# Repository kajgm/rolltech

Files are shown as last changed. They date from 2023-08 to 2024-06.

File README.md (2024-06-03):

# Rolltech - Chairable

Roll Technology presents Chairable, a revolutionary product designed to explore the immature field of spherical wheel technology.

- Chairable utilizes a spherical wheel design for tight maneuvering and a space-efficient footprint
- Leverages an adjustable clamping mechanisim to enable modular attachment to a variety of office chairs
- A large 7000mAh lithium polymer battery and a powerful 2200W motor provide the ability to move a 125kg load at a 2.5m/s pace
- Uses a carefully crafted mechanical design implemented with machined steel and custom 3D printed elements
- A safe and robust experience is achieved through a fully enclosed electrical circuit with 14+ motor control, logic, and safety elements
- Operated remotely using a tailored PCB design, a custom controller casing, and a specifically crafted low-power circuit.

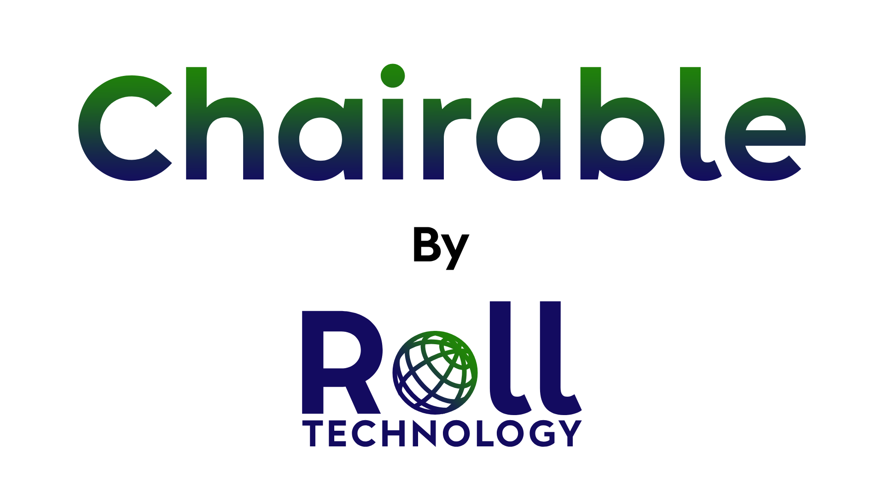
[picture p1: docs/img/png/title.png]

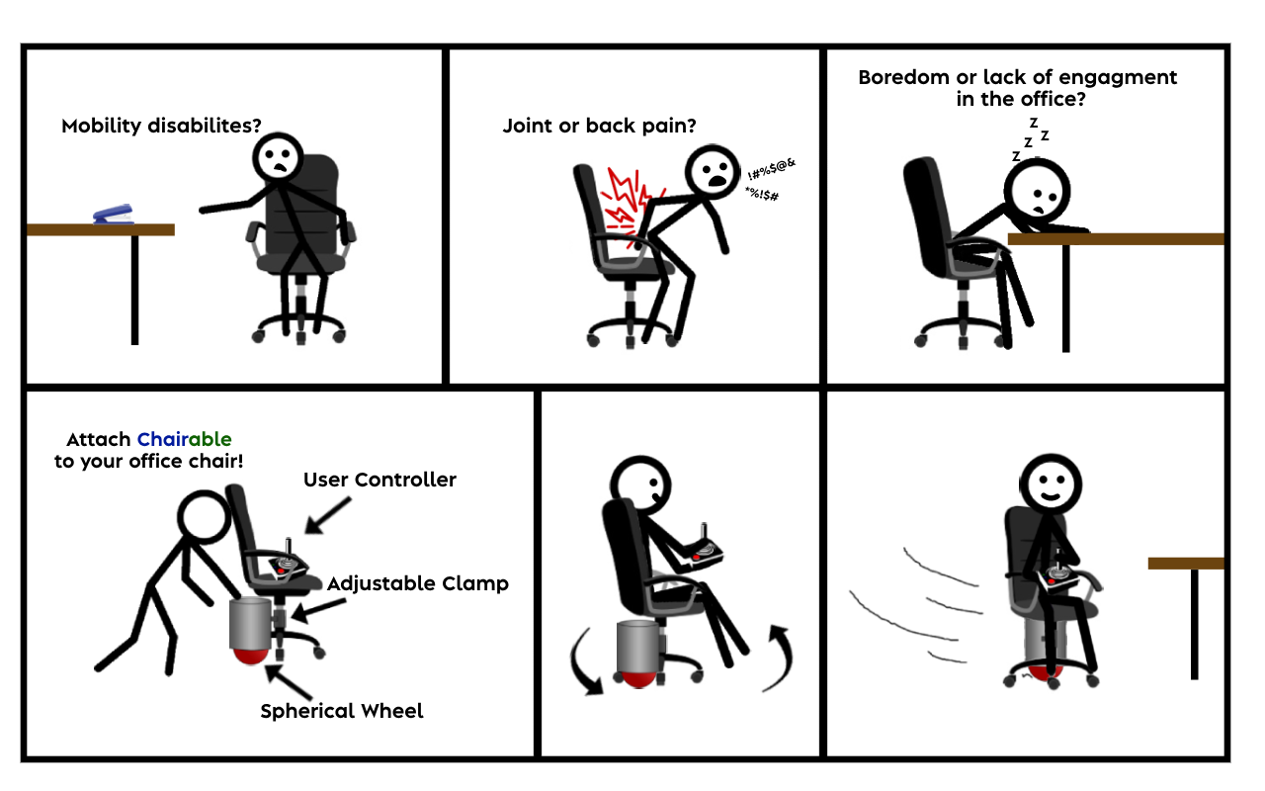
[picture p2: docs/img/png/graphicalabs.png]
Graphical Abstract


## About

Roll Technology is a [Simon Fraser University based Capstone Project](https://summit.sfu.ca/person/81237) group comprised of five 5th year engineering students.

## Folder structure

- PCB - Custom pcb design documents including KiCad schematics
- docs - Design related documentation, company branding, and user manual
- solidworks - Solidworks .STL and .SLDPRT files as well as drawn diagrams
- src - Arduino code relating to the controller device communication and logic

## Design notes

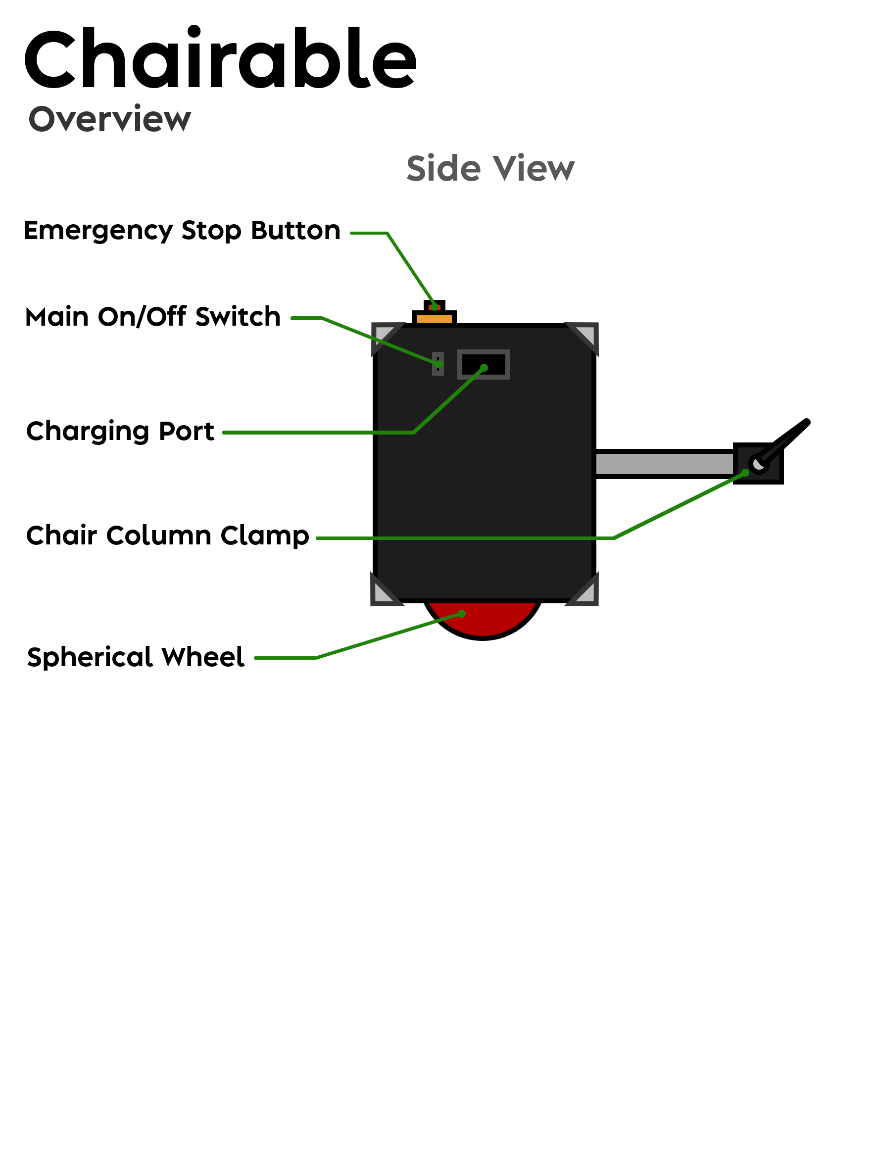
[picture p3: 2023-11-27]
docs/user_manual/png/overview.png

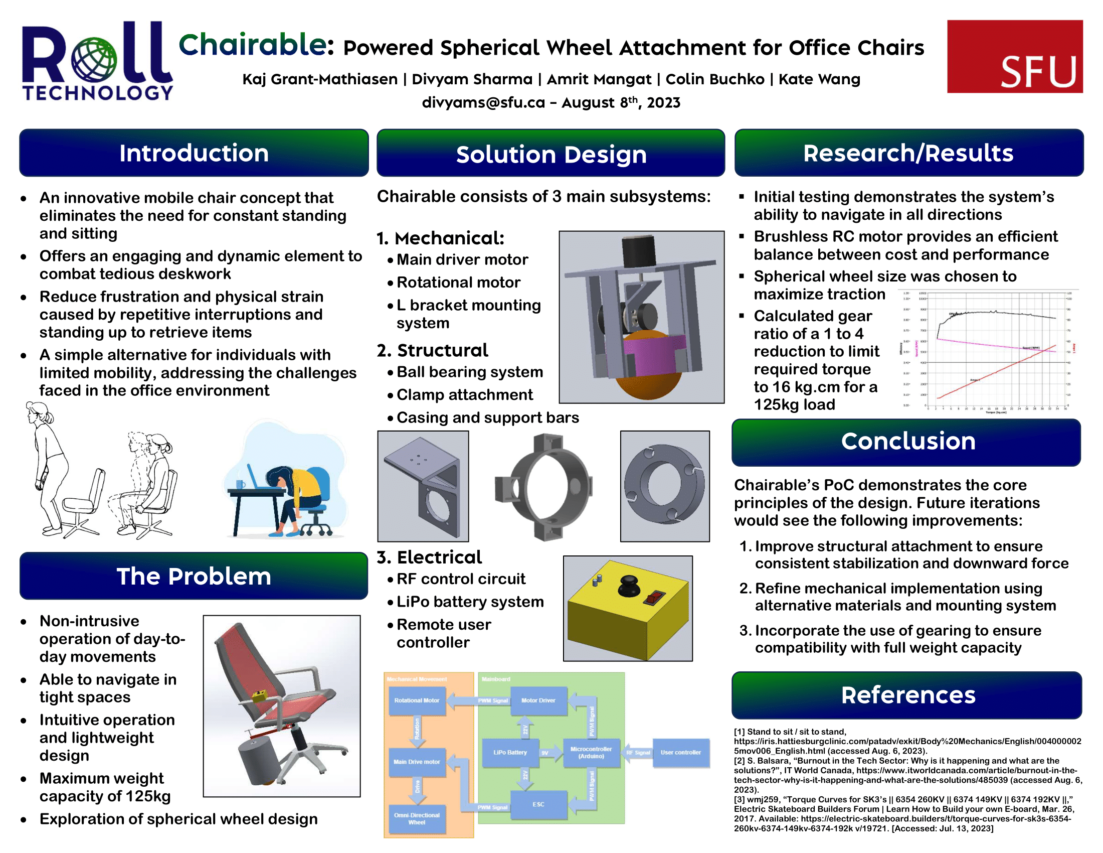
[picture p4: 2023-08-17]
docs/img/poster.png

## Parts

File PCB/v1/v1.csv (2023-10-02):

Source: | C:\Users\Kate Wang\OneDrive\Documents\KiCad\controller\v1\v1.kicad_sch
Date: | 2023-09-27 2:23:12 PM
Tool: | Eeschema 7.0.7
Generator: | C:\Program Files\KiCad\7.0\bin\scripting\plugins/bom_csv_grouped_by_value_with_fp.py
Component Count: | 7
Ref | Qnty | Value | Cmp name | Footprint | Description | Vendor | DNP
D1, D2 | 2 | LED_BGAR | LED_BGAR | LED_THT:LED_D5.0mm-4_RGB_Wide_Pins | RGB LED, blue/green/anode/red
R1, R2 | 2 | R_US | R_US | Resistor_SMD:R_1206_3216Metric | Resistor, US symbol
TB1 | 1 | ARDUINO_NANO | ARDUINO_NANO | ARDUINO_NANO:SHIELD_ARDUINO_NANO
U1 | 1 | NRF24L01_Breakout | NRF24L01_Breakout | RF_Module:nRF24L01_Breakout | Ultra low power 2.4GHz RF Transceiver, Carrier PCB
U2 | 1 | COM-09032 | COM-09032 | COM-09032:XDCR_COM-09032

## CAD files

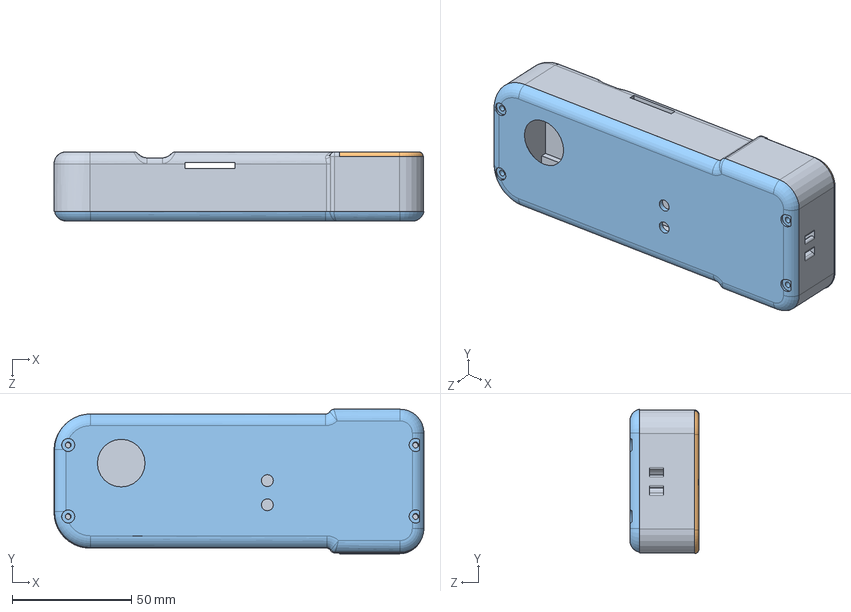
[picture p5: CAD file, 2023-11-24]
solidworks/controller_casing/Assem2.SLDASM
155.2 x 60.7 x 29.1 mm
controller_kaj
controller_kaj_battery
controller_kaj_lid

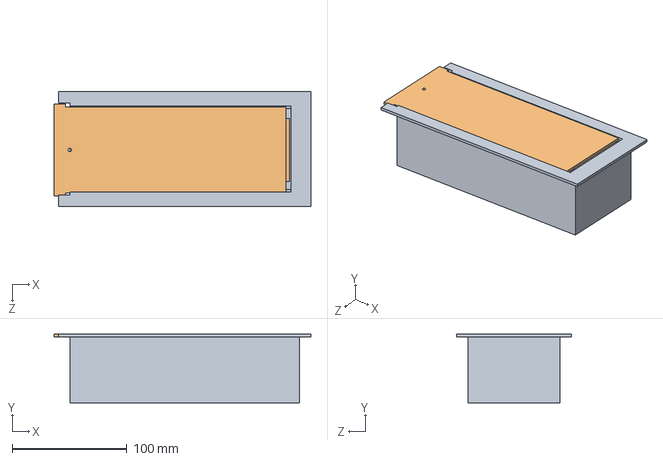
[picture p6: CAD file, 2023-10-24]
solidworks/electronics_casing/Assem1.SLDASM
224.1 x 60.0 x 100.0 mm
battery_housing
lid

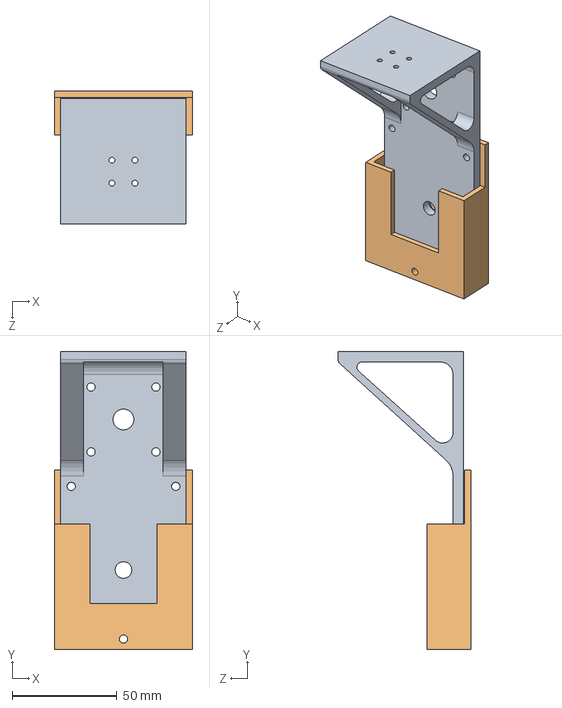
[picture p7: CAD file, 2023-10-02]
solidworks/l_bracket/lbrac+attach_assem.SLDASM
66.0 x 142.5 x 63.6 mm
lbracket_v1
lbrac_attach_v1

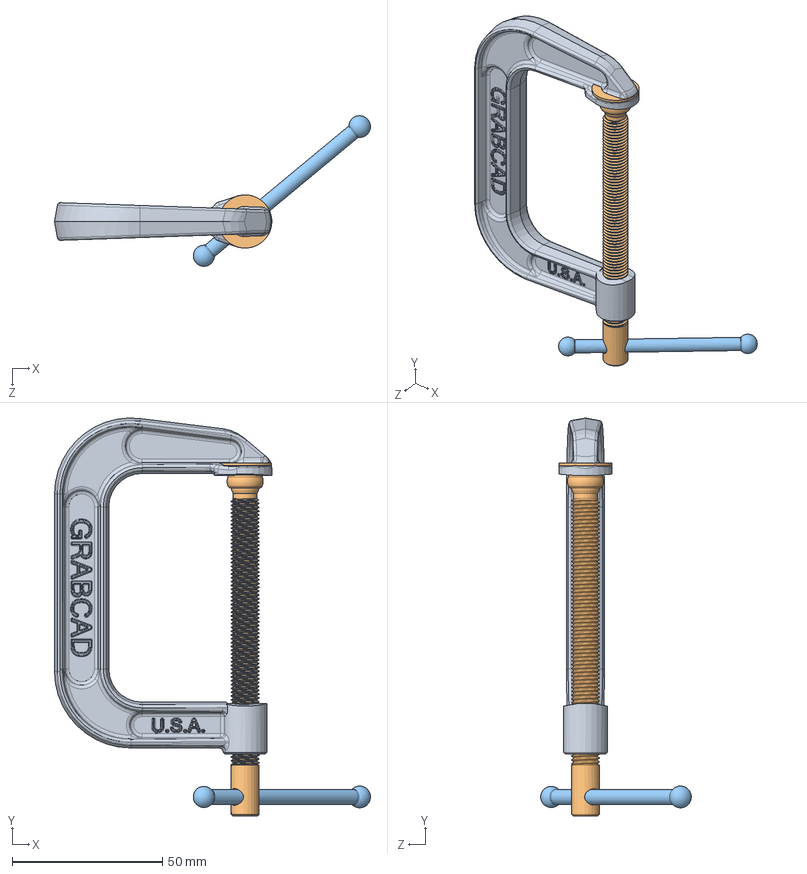
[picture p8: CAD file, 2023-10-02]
solidworks/design/overview/cclamp/C-Clamp, 3in.SLDASM
105.2 x 132.5 x 50.2 mm
C-Clamp body
Screw
Screw, Lever

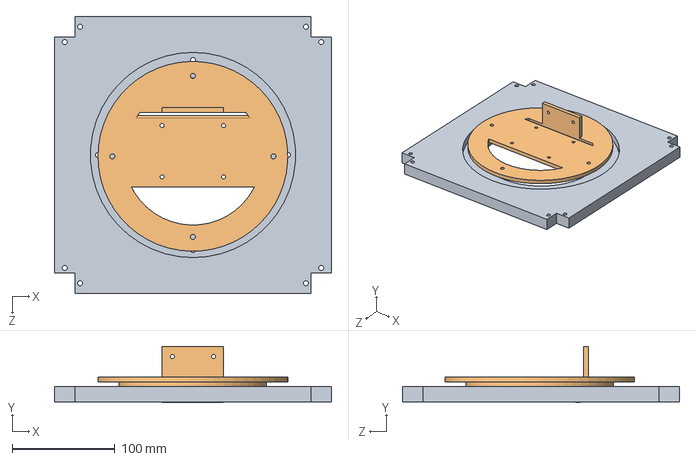
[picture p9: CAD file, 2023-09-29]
solidworks/ring_bracket/ringassembly.SLDASM
270.0 x 55.0 x 270.0 mm
outerring
innerringv2

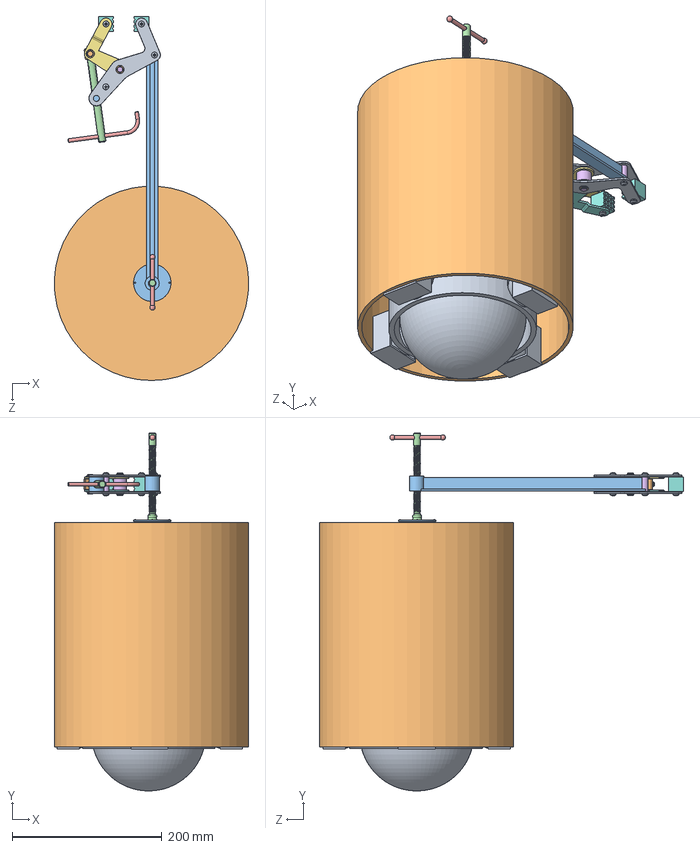
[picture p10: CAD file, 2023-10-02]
solidworks/design/overview/overview/attachment.SLDASM
259.9 x 478.7 x 486.9 mm
interiorattachment
attachmentcap
Screw
Screw, Lever
Clamp hinge
Clamp elbow left
Clamp elbow right
Clamp Base x 2
Clamp Tee
Clamp base spacer
Clamp Rod
Clamp Lever
Clamp base support x 2
Clamp Foot Pin x 2
Clamp Foot x 2
pan head cross recess screw_iso x 8
serrated lock washer 1_din x 5
clampcap

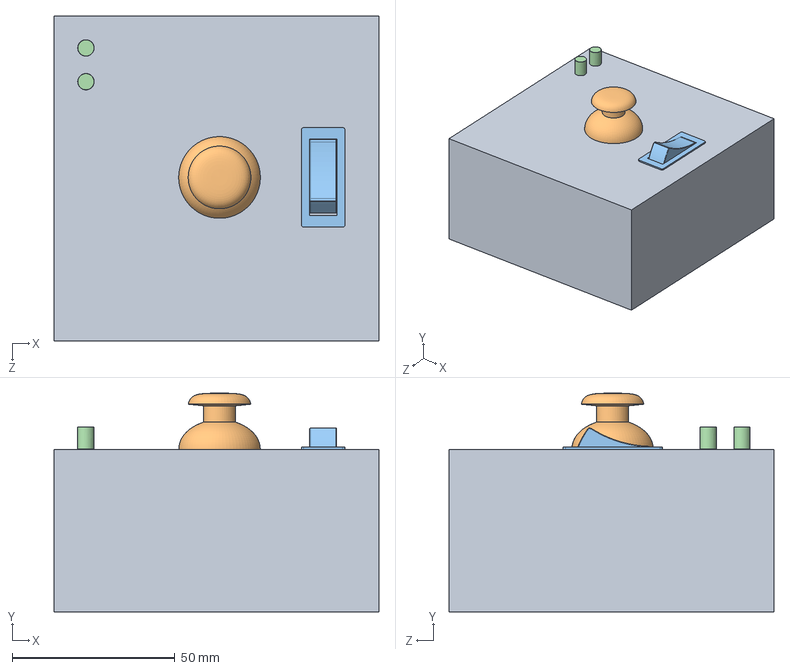
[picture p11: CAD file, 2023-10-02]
solidworks/design/overview/joystick/joystick.SLDASM
100.0 x 67.3 x 100.0 mm
base
PS2 Joystick Module
switch
LUCKYLIGHT LL-504BD2Q-B4-2B v2.step x 2

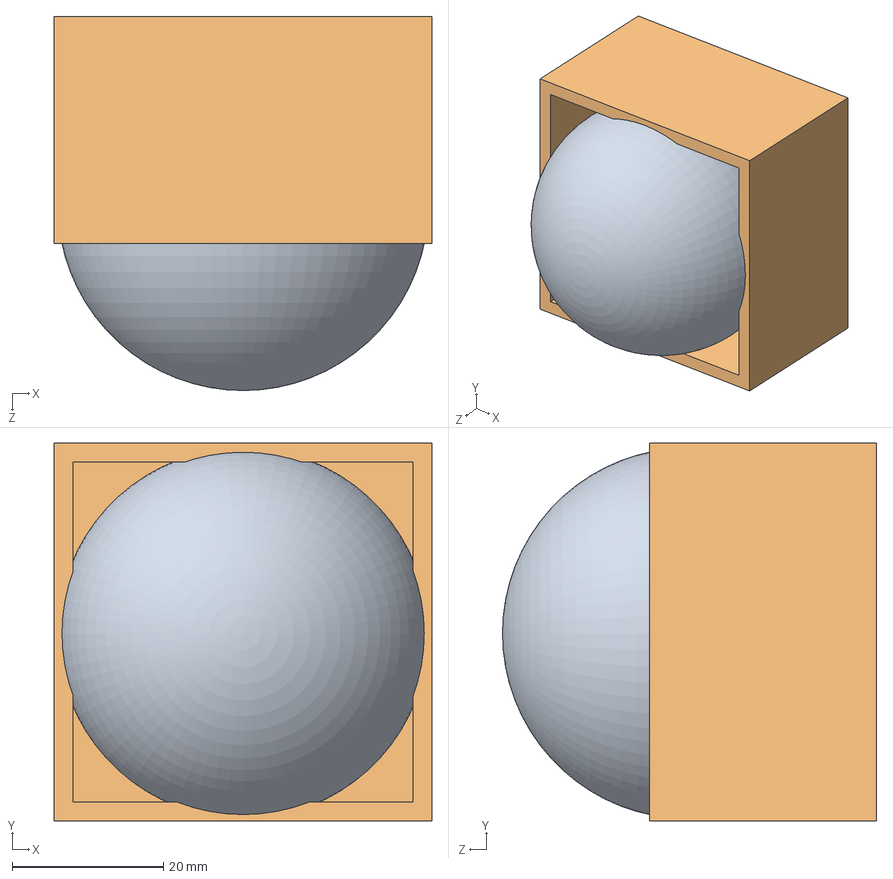
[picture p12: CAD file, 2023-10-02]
solidworks/design/ballframe/BearingContainerAsm.SLDASM
50.0 x 50.0 x 49.5 mm
miniball
container

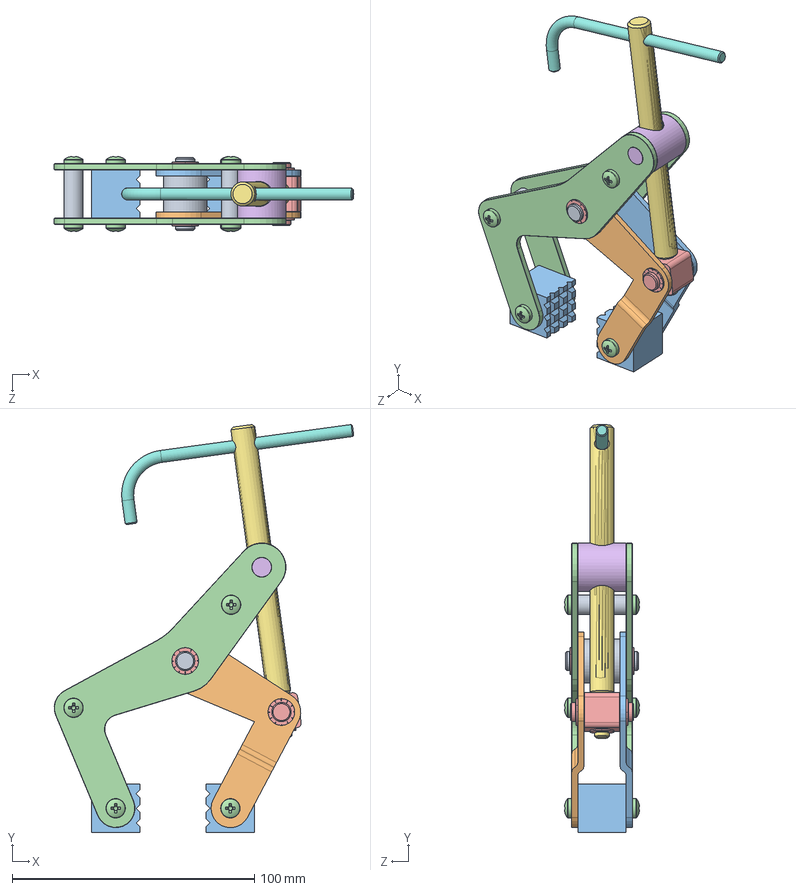
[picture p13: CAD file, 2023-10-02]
solidworks/design/overview/clampchair/Manual Clamp Assembly.SLDASM
123.7 x 168.5 x 31.0 mm
Clamp hinge
Clamp elbow left
Clamp elbow right
Clamp Base x 2
Clamp Tee
Clamp base spacer
Clamp Rod
Clamp Lever
Clamp base support x 2
Clamp Foot Pin x 2
Clamp Foot x 2
pan head cross recess screw_iso x 8
serrated lock washer 1_din x 5

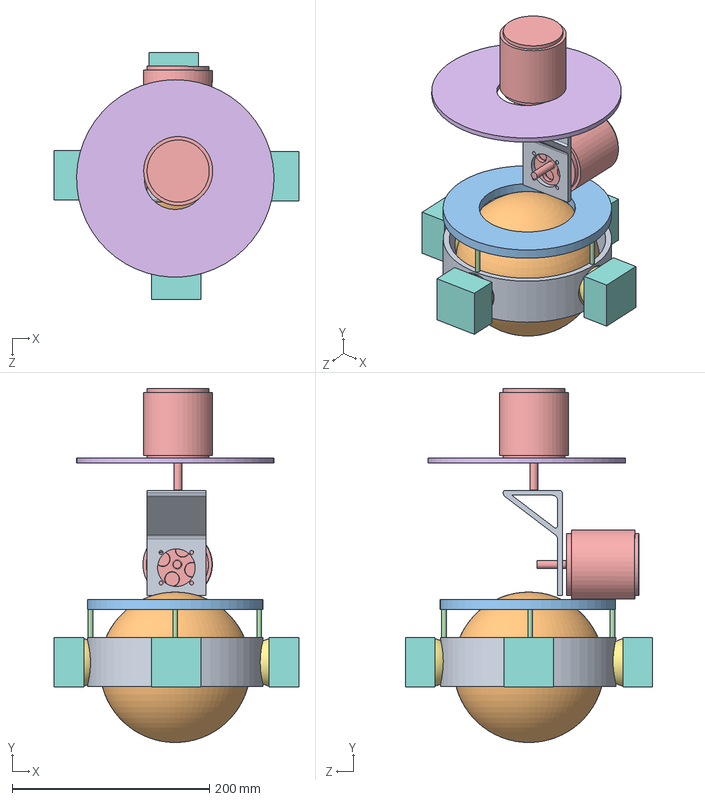
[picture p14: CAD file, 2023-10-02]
solidworks/design/ballframe/BASEFRAME.SLDASM
247.8 x 358.6 x 250.3 mm
Ring
Ball
topring
ringsupport x 4
motormodel x 2
uppercasing
miniball x 4
container x 4
lbrac_v2

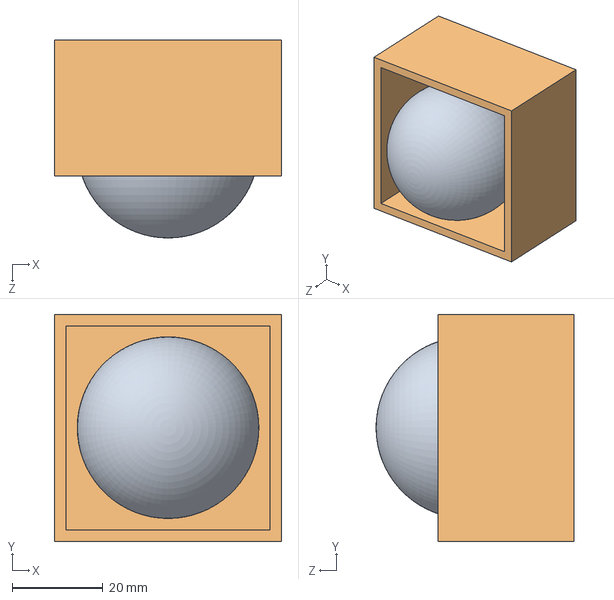
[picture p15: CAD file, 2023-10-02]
solidworks/design/ballframe_poc/BearingContainerAsm.SLDASM
50.0 x 50.0 x 43.6 mm
miniball
container

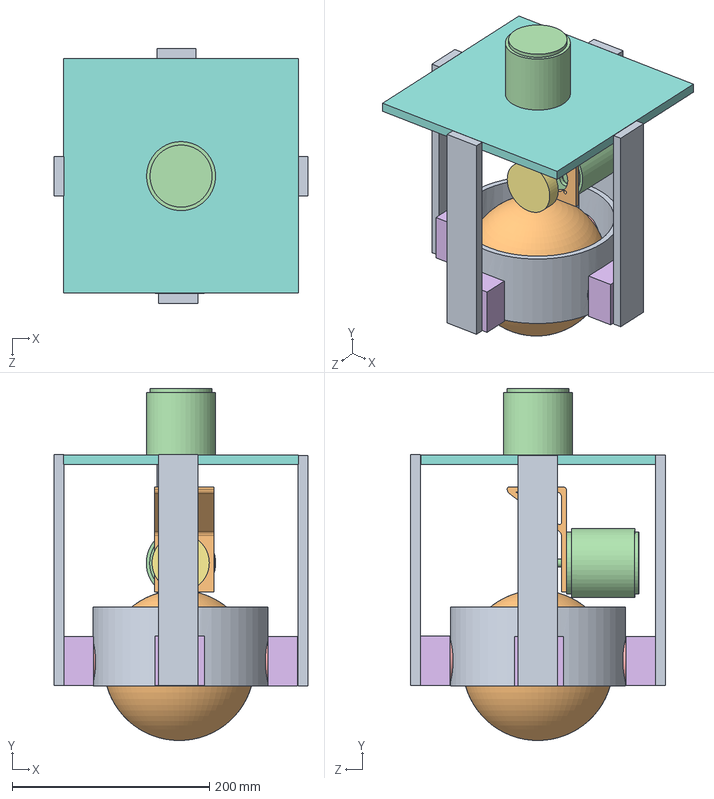
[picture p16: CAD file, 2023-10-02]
solidworks/design/ballframe_poc/BASEFRAME.SLDASM
257.4 x 356.8 x 258.4 mm
Ring
Ball
ringsupport x 2
motormodel x 2
miniball x 4
container x 4
wheeeeel
topsquare
woodbarsupport x 4
lbrac_v2

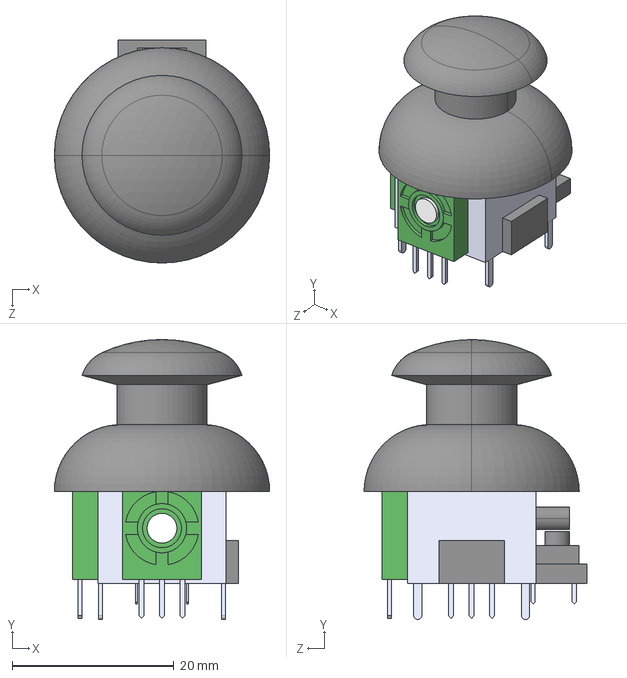
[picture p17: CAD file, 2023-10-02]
PCB/v1/joystick/COM-09032.step
26.7 x 34.7 x 27.6 mm

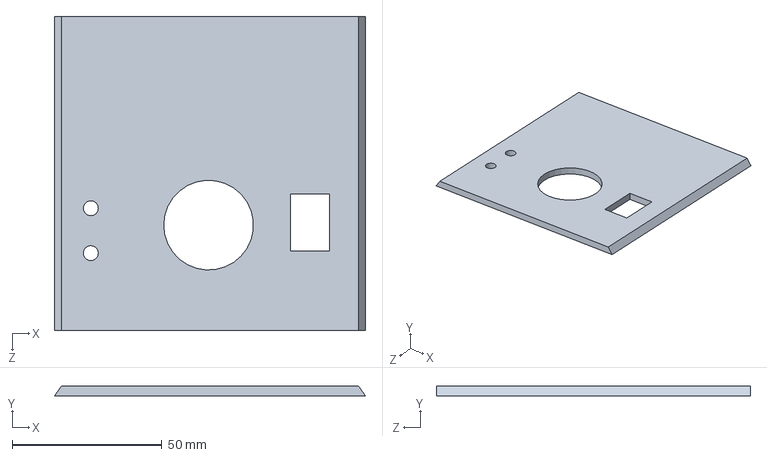
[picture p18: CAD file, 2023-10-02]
solidworks/controller_box/SLDPRT/cover_v3.SLDPRT
104.0 x 3.28 x 105.0 mm

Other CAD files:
solidworks/controller_casing/SLDPRT/ucase_v4.SLDPRT
solidworks/design/ballframe/Ring.SLDPRT
solidworks/design/ballframe_poc/topring.SLDPRT
solidworks/design/chair/Part2.SLDPRT
solidworks/controller_box/SLDPRT/box.SLDPRT
solidworks/controller_box/STL/box.STL
solidworks/controller_box/STL/cover_v3.STL
solidworks/controller_casing/SLDPRT/controller_v1.SLDPRT
solidworks/controller_casing/SLDPRT/controller_v2.SLDPRT
solidworks/controller_casing/SLDPRT/controller_v3.SLDPRT
solidworks/controller_casing/SLDPRT/controller_v4.SLDPRT
solidworks/controller_casing/SLDPRT/controller_v5.SLDPRT
solidworks/controller_casing/SLDPRT/controller_v6.SLDPRT
solidworks/controller_casing/SLDPRT/controller_v7.SLDPRT
solidworks/controller_casing/SLDPRT/lcase_v1.SLDPRT
solidworks/controller_casing/SLDPRT/lcase_v2.SLDPRT
solidworks/controller_casing/SLDPRT/lcase_v3.SLDPRT
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

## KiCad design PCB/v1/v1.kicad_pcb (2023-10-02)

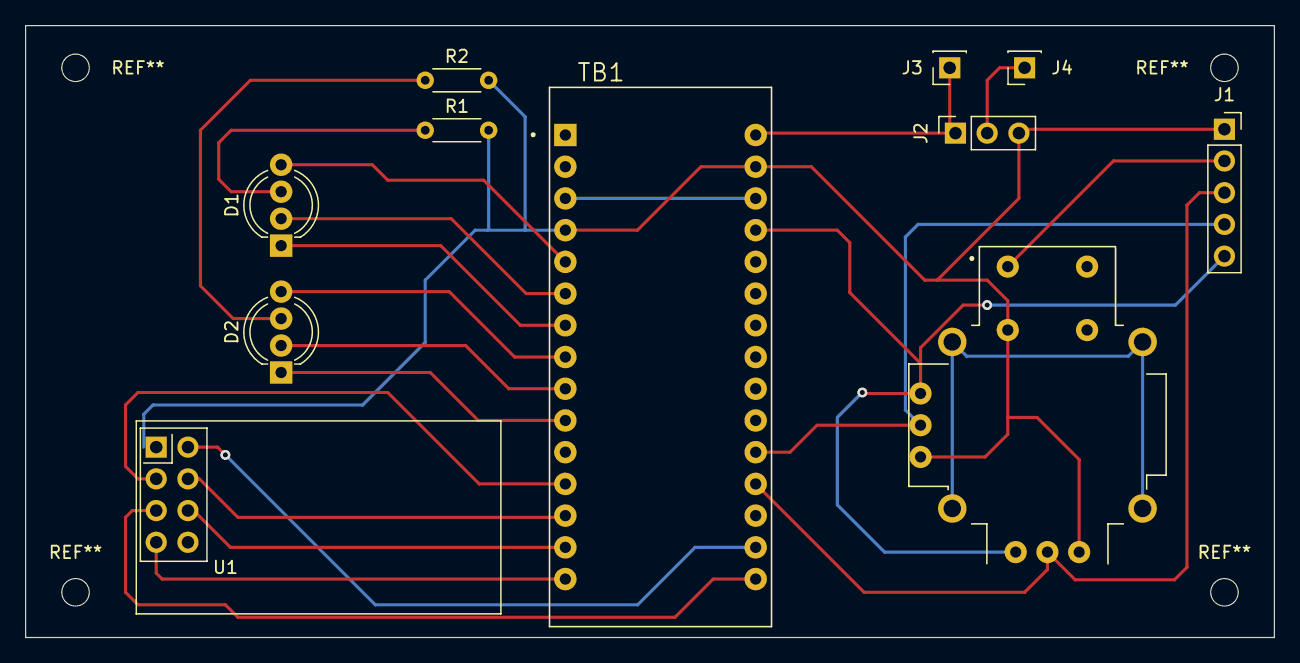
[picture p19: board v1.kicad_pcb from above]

Board: 2 copper layers, 100.0 x 49.0 mm, 11 parts (0 on the bottom side), 21 nets.

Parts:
D1, D2: LED_BGAR; LED_D5.0mm-4_RGB_Wide_Pins
J1: Conn_01x05; PinSocket_1x05_P2.54mm_Vertical
J2: Conn_01x03; PinSocket_1x03_P2.54mm_Vertical
J3, J4: Conn_01x01; PinSocket_1x01_P2.54mm_Vertical
R1, R2: R; R_Axial_DIN0204_L3.6mm_D1.6mm_P5.08mm_Horizontal
TB1: ARDUINO_NANO; SHIELD_ARDUINO_NANO
U1: NRF24L01_Breakout; nRF24L01_Breakout
U2: COM-09032; XDCR_COM-09032

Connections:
GND: J1.1, J2.3, R1.2, R2.2, TB1.4 (COM/GND), TB1.29 (COM/GND), U1.1 (GND), U2.B2A (SEL-), U2.H3 (H-), U2.V3 (V-)
unnamed: D1.3 (A), R1.1
unnamed: D1.1 (BK), TB1.7 (D4)
unnamed: D1.2 (GK), TB1.6 (D3)
unnamed: D1.4 (RK), TB1.5 (D2)
unnamed: D2.3 (A), R2.1
unnamed: D2.1 (BK), TB1.10 (D7)
unnamed: D2.2 (GK), TB1.9 (D6)
unnamed: D2.4 (RK), TB1.8 (D5)
unnamed: J1.2, U2.B1A (SEL+)
unnamed: J1.3, TB1.19 (A0), U2.H2 (H)
unnamed: J1.4, TB1.20 (A1), U2.V2 (V)
unnamed: J1.5, TB1.27 (+5V), U2.H1 (H+), U2.V1 (V+)
unnamed: J2.1, J3.1, TB1.30 (VIN)
unnamed: J2.2, J4.1
unnamed: TB1.17 (3V3), U1.2 (VCC)
unnamed: TB1.12 (D9), U1.3 (CE)
unnamed: TB1.13 (D10), U1.4 (~CSN)
unnamed: TB1.14 (D11/MOSI), U1.6 (MOSI)
unnamed: TB1.15 (D12/MISO), U1.7 (MISO)
unnamed: TB1.16 (D13/SCK), U1.5 (SCK)

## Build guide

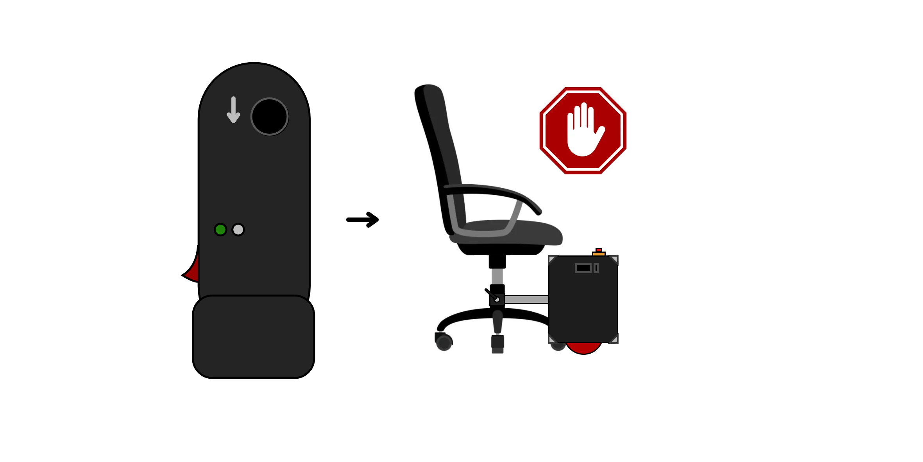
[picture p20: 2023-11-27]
docs/user_manual/png/op_step7.png

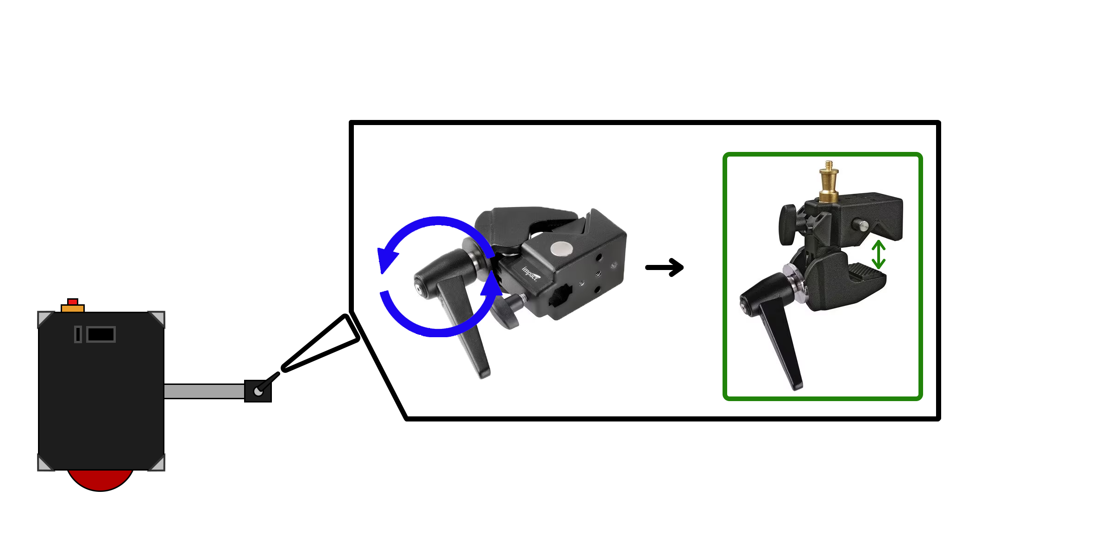
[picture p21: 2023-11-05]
docs/user_manual/png/step2.png

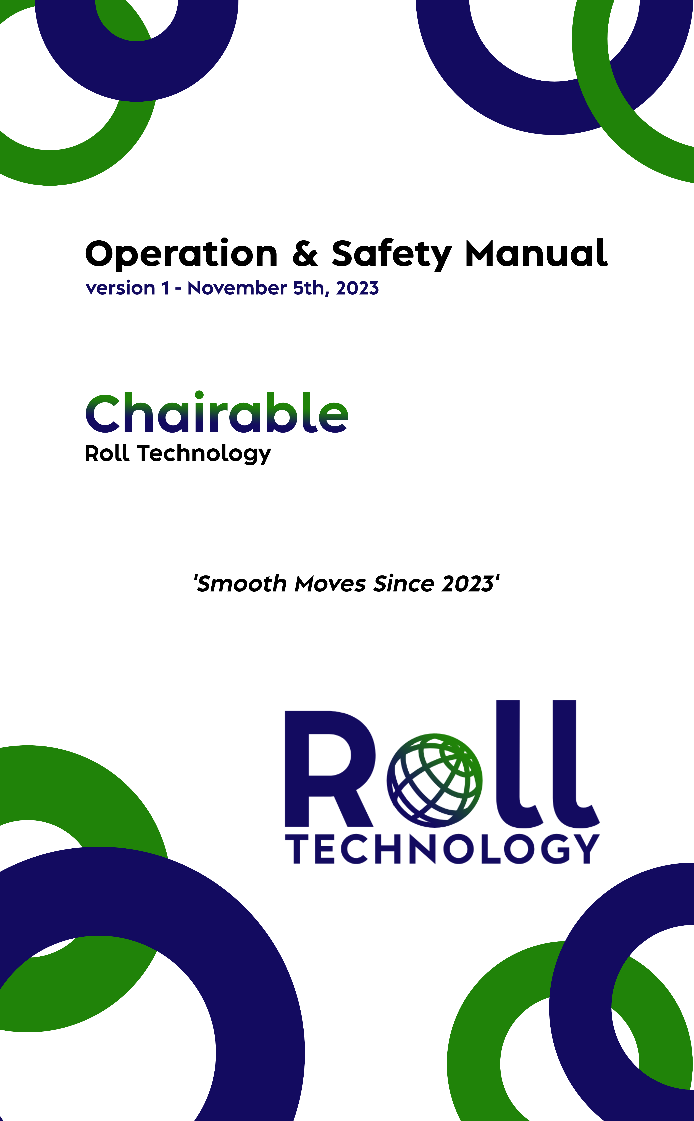
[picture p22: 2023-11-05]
docs/user_manual/png/operation_manual_titlepage.png

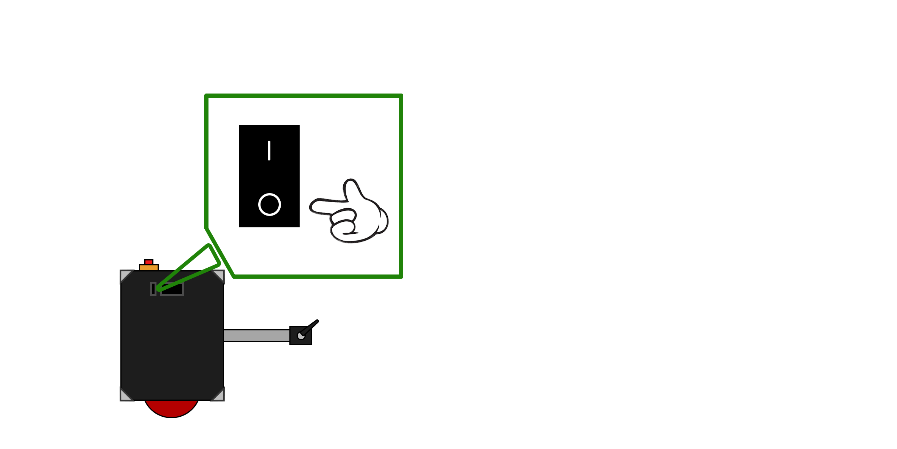
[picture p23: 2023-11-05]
docs/user_manual/png/op_step8.png

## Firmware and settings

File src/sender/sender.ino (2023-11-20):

/*
* Arduino Wireless Communication Tutorial
*     Example 1 - Transmitter Code
*                
* by Dejan Nedelkovski, www.HowToMechatronics.com
* 
* Library: TMRh20/RF24, https://github.com/tmrh20/RF24/
*/

#include <SPI.h>
#include <nRF24L01.h>
#include <RF24.h>

#define inX 0 //Joystick X input
#define inY 1 //Joystick Y input

#define RED_PIN1 5
#define GREEN_PIN1 6
#define BLUE_PIN1 7

#define RED_PIN2 2
#define GREEN_PIN2 3
#define BLUE_PIN2 4

RF24 radio(9, 10); // CE, CSN

const byte address[6] = "00001";
int buffer[2];

void setup() {
  Serial.begin(19200);
  radio.begin();
  radio.openWritingPipe(address);
  radio.setPALevel(RF24_PA_MIN);
  radio.stopListening();

  //setup led pins 1 and 2
  pinMode(RED_PIN1, OUTPUT);
  pinMode(GREEN_PIN1, OUTPUT);
  pinMode(BLUE_PIN1, OUTPUT);

  pinMode(RED_PIN2, OUTPUT);
  pinMode(GREEN_PIN2, OUTPUT);
  pinMode(BLUE_PIN2, OUTPUT);

  //set leds to off
  digitalWrite(RED_PIN1, LOW);
  digitalWrite(GREEN_PIN1, LOW);
  digitalWrite(BLUE_PIN1, LOW);

  digitalWrite(RED_PIN2, LOW);
  digitalWrite(GREEN_PIN2, LOW);
  digitalWrite(BLUE_PIN2, LOW);

}

void loop() {
  //assume full charge -will need to change
  digitalWrite(GREEN_PIN2, HIGH);

  int potValueX = analogRead(inX); 
  int pwmOutputX = map(potValueX, 0, 1023, 0, 120); 

  int potValueY = analogRead(inY); 
  int pwmOutputY = map(potValueY, 0, 1023, 45, 135); 


  if (abs(pwmOutputX-60) <= 20 && pwmOutputY<80){
    //Forward
    buffer[0] = 60;
    buffer[1] = 70;
    Serial.println("Forward");
  } else if (abs(pwmOutputX-60) <= 20 && pwmOutputY>100) {
    //Backward
    buffer[0] = 60;
    buffer[1] = 110;
    Serial.println("Backward");
  } else if (pwmOutputX > 80 && abs(pwmOutputY-90) <= 20) {
    // right
    buffer[0] = 120;
    buffer[1] = 60;
    Serial.println("right");
  } else if (pwmOutputX < 40 && abs(pwmOutputY-90) <= 20) {
    //left
    buffer[0] = 0;
    buffer[1] = 60;
    Serial.println("left");
  } else if (pwmOutputX > 80 && pwmOutputY < 70) {
    //forward right
    buffer[0] = 90;
    buffer[1] = 60;
    Serial.println("forward right");
  } else if (pwmOutputX < 40 && pwmOutputY < 70) {
    //forward left
    buffer[0] = 30;
    buffer[1] = 60;
    Serial.println("forward left");
  } else if (pwmOutputX > 80 && pwmOutputY > 110) {
    //backward right
    buffer[0] = 30;
    buffer[1] = 120;
    Serial.println("backward right");
  } else if (pwmOutputX < 40 && pwmOutputY > 110) {
    //backward left
    buffer[0] = 90;
    buffer[1] = 120;
    Serial.println("backward left");
  } else {
    // No movement
    buffer[0] = 60;
    buffer[1] = 90;
    Serial.println("No movement");
  }

  radio.write(&buffer, sizeof(buffer));
  
  // Serial.print("x:");
  // Serial.print(pwmOutputX);
  // Serial.print(" y:");
  // Serial.println(pwmOutputY); 
}

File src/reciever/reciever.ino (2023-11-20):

#include <SPI.h>
#include <nRF24L01.h>
#include <RF24.h>
#include <Servo.h>

RF24 radio(7, 8); // CE, CSN

Servo ESC;
Servo myservo;
int pos = 60;

const byte address[6] = "00001";

int pwmOutputX;
int pwmOutputY;
int potVals[2];

void setup() {
  Serial.begin(9600);

  // Set motors to stop initially
  myservo.attach(3);
  myservo.write(pos);

  ESC.attach(2, 1000, 3000);
  ESC.write(90);

  pwmOutputX = pos;
  pwmOutputY = 90;

  radio.begin();
  radio.openReadingPipe(0, address);
  radio.setPALevel(RF24_PA_MIN);
  radio.startListening();
}

void loop() {
  if (radio.available()) {
    radio.read(&potVals, sizeof(potVals));
    //Serial.println(potVals);

    pwmOutputX = potVals[0];
    pwmOutputY = potVals[1];

    myservo.write(pwmOutputX);
    ESC.write(pwmOutputY);

  } else {
    ESC.write(90);
    myservo.write(60);
  }

  delay(50);
  Serial.print("x:");
  Serial.print(pwmOutputX);
  Serial.print(" y:");
  Serial.println(pwmOutputY); 
}

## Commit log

2023-06-22 feat: initial arduino sketch
2023-06-25 added dual motor functionality with joystick
2023-07-02 poc circuit for demo day
2023-07-18 added LED signalling
2023-07-25 added support for main driver motor
2023-09-06 added final 405 docs
    [circuit.fzz]
2023-09-10 next iteration of part schematics
    [circuit.fzz]
2023-09-15 updated schematics
2023-09-18 revert speed adjustments and doc updates
    [sender.ino]
2023-09-26 new schematics
2023-09-29 ring bracket schematics
    [Assem1.SLDASM, innerring.SLDPRT, innerring.STL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]
2023-09-29 fixes to ring schematic
    [innerringv2.SLDPRT, innerringv2.STL, outerring.SLDPRT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]
2023-10-02 Create controller
    PCB files for controller
2023-10-02 Add files via upload
    All the pcb files
    [COM-09032.step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]
2023-10-02 file structure refactor
    [innerring_v2.SLDPRT, innerring_v2.STL, outerring.SLDPRT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]
2023-10-02 Added all of the solidworks files
    [BASEFRAME.SLDASM, BASEFRAME.SLDDRW, BASEFRAME.SLDPRT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]
2023-10-02 refactor of file structure
    [BASEFRAME.SLDASM, BASEFRAME.SLDDRW, BASEFRAME.SLDPRT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]
2023-10-08 updated schematics with final design
    [box.SLDPRT, box.STL, clip_v1.SLDPRT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]
2023-10-24 updated models and circuit diagram
    [Assem1.SLDASM, battery_housing.SLDPRT, battery_housing.STL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]
2023-11-04 user manual diagrams
    [battery_ports.SLDPRT, battery_ports.STL, battery_stand.SLDPRT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]
2023-11-12 init 3d model for controller casing
    [controller_v1.SLDPRT, controller_v1.STL]
2023-11-14 Added v2 of controller casing body
    [controller_v2.SLDPRT, controller_v2.STL]
2023-11-14 Added rounded corners for casing bracket
    [controller_v3.SLDPRT]
2023-11-14 Added STL v3 controller casing with rounded edges
    [controller_v3.STL]
2023-11-19 fixed up rotation issue
    [reciever.ino]
2023-11-19 Added more versions of the controller casing
    [controller_v4.SLDPRT, controller_v4.STL, controller_v5.SLDPRT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]
2023-11-20 3D Modelled More Casing Part
    [lcase_v1.SLDPRT, lcase_v1.STL, ucase_v1.SLDPRT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]
2023-11-20 3D Models of More Controller casing
    [controller_v6.SLDPRT, controller_v6.STL, lcase_v2.SLDPRT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]
2023-11-20 [SOFTWARE] Minor improvements to jitter due to input
    [reciever.ino, sender.ino]
2023-11-24 improved case
    [Assem2.SLDASM, controller_kaj.SLDPRT, controller_kaj_battery.SLDPRT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]
2023-11-24 Minor update on controller body and rename
    [controller_kaj.SLDPRT, controller_v7.SLDPRT, controller_v7.STL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]
2023-11-27 updates to controller casing and user manual pictures
    [controller_v7.SLDPRT, controller_v7.STL, lcase_v3.SLDPRT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]
